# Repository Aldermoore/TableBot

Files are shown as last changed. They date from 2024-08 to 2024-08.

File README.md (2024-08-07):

# TableBot

Repo for the final code, 3d-models and assembly instructions for the TableBot tabletop telepresence robot

**Table of content**

[Components needed](#components-needed)

* [Electronics](#electronics)
* [Hardware](#hardware)
* [Files to 3D print](#files-to-3d-print)

[Assembly instructions](#assembly-instructions)

* [Assembling the head](#assembling-the-head)
* [Assembling the base](#assembling-the-base)

[Installation](#installation)

[Configuration and Running the software](#configuration-and-running-the-software)

<small><i><a href='http://ecotrust-canada.github.io/markdown-toc/'>Table of contents generated with markdown-toc</a></i></small>

---

# ⚠️ **DISCLAIMER: We provide no guarantee that you will produce a working product from following these instructions!**

---

## Components needed

### Electronics

* Raspberry Pi 4

* 7'' touchscreen for Raspberry Pi 

* 180° fish-eye lens USB camera, model ELP-USBFHD01M-L180 

* Jabra Speak 510 conference microphone and speaker

* Servo RDS3115mg

* Stepper Motor 17HS4401 x2

* Adafruit motor shield V1 (V1 is discontinued, use V2 instead at your own risk)

* Arduino Uno

* RGB LED-strip

* Power Banks 5000mAh 2.5A x3 (TB is designed for quite flat batteries, but the battery compartment can be modified to accomodate other battery shapes)

* USB-A cables to connect powerbanks to electronics (these will be cut open during assembly!) 

* A few basic electronic components; Capacitor, diode, breadboard/soldering-board, Jumperwires

### Hardware

* 3D-printer (Prusa Mini or larger) 

* Access to soldering equipment

* Access to silicone casting to create tires

* Tabletop-tennis ball (for the castor wheel)

* Screws and appropriate screwdriver
  
  * Assorted screws for electronics (see pictures)
20240806_121625 (1)
20240806_121608 (1)
20240806_121558 (1)
20240806_121548 (1)
20240806_121401 (1)


## Files to 3D print

All 3d files to build TableBot are available in the TableBot_stl folder. All files should only be printed once, except for the wheels (you might prefer to have two of those).

The wheels have silicone tires, and the folder Silicone_mould includes the necessary files. To produce the mould, print one of each piece. Connect all pieces with a wheel base as the centre, close outer gaps with tape and pour in your silicone mixture. Let the silicone set for some time. Pull apart the mould and repeat for the second wheel.

The original TableBot is printed primarily in PLA, but a few pieces are printed in PETG for better heat resistance and flexibility. This includes:
* Arduino_mount.stl
* RaspberryPi_mount.stl
* Screen_grid.stl

The Diffuser_Plane.stl file should be printed in a clear material to allow light through it.

## Assembly instructions

To build the robot, please have the 3d printed files ready and without supports. The following images may include 3d printed elements that differ from those in the included files, as the files offered in this repository has been updated with any changes made to those shown in the images.

First, build the head, then the base and put the two together in the end.

### Assembling the head
Place nuts in assigned slots on the grid

Attach servo arm using four bolts


Attach the grid to the back of the screen in eight spots

Attach holder for Raspberry Pi using the screws for the heat sink. Use four small nuts to as spacers to ensure the plastic does not touch the Raspberry Pi directly


Connect the display cable to the screen


Flip the Raspberry Pi and connect it to the grid using two bolts


Place the screen in the 3d printed frame. Use four bolts to keep it in place

Install the camera by placing it in the assigned space and use two small screws to keep it in place


Leave the head for now as we build the main body
### Assembling the base
Pad the stepper motors with some felt to reduce vibrations and place them in the assigned slots.


Place four nuts in the assigned spots inside the bottom of the handle.

The neck must be fully wired before attached to the body. Prepare the Jabra speaker, the servo motor, a data cable for the Arduino, a power cable for the Raspberry Pi and a length of male/female jumper wires for the LED strip, one for data, one for power and one for ground.

Before wiring the handle, the Jabra speaker needs to have its wire moved from the front to the back of the main body.

Now send all wires through the handle. Ensure the top of the handle has the wires as shown on the following image. The wire for the servo motor must be moved through the handle to the bottom of the handle.

Before connecting the handle to the base, move the LED jumper wires through the hole in the base of the main body.

Slid the handle into the groved on the top of the main body and secure it using two bolts.

Pull the power cable for the Raspberry Pi through the hole in the bottom of the main body.

Prepare the Arduino motor driver shield.


Combine the 3d printed Arduni base with the Arduino and shield.


Slide the Arduino onto the main body.

Up next secure the connection between the power and Servo motor using a flyback diode.


Connect the servo motor to the Arduino motor driver shield through the flyback diode.

Tug the loose wires into the space below the handle.

Under the main body, pull the power supply chords for the Arduino and Servo motor through the same hole as the power cable for the Raspberry Pi.

Next, prepare the side covers for the main body.

Pull the wires for the wires for the stepper motors through the hole underneath the side piece. Connect them with the closest free wires from the Arduino motor shield by matching the colours.

To secure the side cover, slide it into place while pulling the wires out of the way. Repeat on the other side.

Tug the loose wires into the space above the stepper motors.

At the front of the main body, prepare 3d prints and an LED strip.

Place the LED strip within the slot on the solid piece. To help it along, shape the LED strip through small bends.

Place the 3d printed piece with the LED strip on the front of the main body. Make sure the wires for the LED strip face the centre of the front area when placing it. Connect the LED strip with the jumper wires.


Tug the wires away along the side and place Jabra speaker in the assigned slot with its wires rolled up around its base.

Lightly place the diffuser piece over the LEDs.

Attach the large wheels to the stepper motors.

Underneath the robot attach the ball wheel base with two short wood screws. Once in place, insert the ping-pong ball.


Prepare the back piece and two bolts.

Slide the back piece in place and secure it with the two bolts


Attach the head to the body of the robot using the servo arm and the accompanying bolts. Connect all cables and wires to the Raspberry Pi.

Prepare the back of the head and secure it using four small bolts.


In the front, ensure the jumper wires for power to the Arduino and Servo have USB ends. Insert the three power banks into the slots in the front of the main body.

Connect a power bank to each wire.

Close the drawer while tugging any remaining lose wires into the drawer space.

### Attach the head



## Installation

Flash the code in `code / motorcontroller` to the Arduino Uno. 

The remaining code must be moved to the Raspberry Pi. Using git, make sure to clone into the home folder! 

Follow the build and install instructions in `code / video4linux-custom`

From `code / video4linux-custom` run the script called `setupeverything.sh`. 
**NOTE:** The script expects that the path to the files is `~/TableBot/code/front-end-webrtc/server.sh` and `~/TableBot/code/websocket-server/websocketServer.py`. If you have not cloned the repo to the home folder, or have used other means to move the code to the Raspberry Pi, then update the paths on lines 14 and 15 in the `setupeverything.sh` script to reflect this change! 

## Configuration and Running the software

Connect a keyboard and mouse to the Raspberry Pi. 

Connect the Pi to your Wifi network. Note the IP address of the Pi. 

Run the `setupEverything.sh` script. 

In a browser (Tested with Google Chrome, not working with Firefox!), go to the Pi's IP address, port 5

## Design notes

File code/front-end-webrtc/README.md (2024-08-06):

# uv4l-webrtc-front-end

UV4L Webrtc Front-End Source Code

Original source code of UV4L WebRTC front end. No code changes, only split html, js and css. Original code by [https://www.linux-projects.org](https://www.linux-projects.org/)

This code should be downloaded to the Raspberry Pi used in TableBot! 

#

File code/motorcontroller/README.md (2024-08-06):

# Motor-Controller

Motor controller code for Arduino. The code assumes that the Adafruit Motor Shield (AMS) V1 is connected to the arduino, and that the motors are wired as described below. 

**It is NOT tested with the Motor Shield V2**

## Overview of files

`tablebotWheelset/tablebotWheelset.ino` is the one that should be uploaded to the Arduino to work with TableBot. 

## Wiring Arduino and motors

1. Connect the arduino motor shield to the arduino

2. Connect the stepper motors in the following way
   
   1. Left stepper is connected to M3 & M4, while right stepper is connected to M1 & M2. 
   
   2. With the specific set of motor terminals facing you, the steppers are wired up in the order: 
      Orange, Brown, Red, Yellow
      So the leftmost terminal connects the orange wire on the stepper, while the rightmost terminal connects the yellow wire on the stepper. Fuck this up and the steppers will *not* drive correctly! 
   
   3. Left stepper obviously need to be on the left side of the robot chassis (duh) 

3. Connect the servo to the first servo port labeled SER1 or SERVO_1 or similar.

4. You should be all done for now, except for the fact that the steppers draw too much power so they might shut down the arduino which is kind of a problem for future us...

## Powering the motors

The steppers can be powered from external power via the `EXT_PWR`  connectors. Wire up a bettery to this port, e.g. by cutting a USB-cable and soldering some jumper wire ends to the power and ground leads of the cable. 

Additionally the `PWRJMP` jumper should be removed from the board when using external power.

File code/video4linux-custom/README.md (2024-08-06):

v4l2loopback - a kernel module to create V4L2 loopback devices
==============================================================

This module allows you to create "virtual video devices".
Normal (v4l2) applications will read these devices as if they were ordinary
video devices, but the video will not be read from e.g. a capture card but
instead it is generated by another application.
This allows you for instance to apply some nifty video effects on your
Skype video...
It also allows some more serious things (e.g. I've been using it to add
streaming capabilities to an application by the means of hooking GStreamer into
the loopback devices).

# NEWS

To get the main features of each new release, see the NEWS file.
You could also have a look at the ChangeLog (which gets automatically generated and might
only be of limited use...

# ISSUES

For current issues, checkout https://github.com/umlaeute/v4l2loopback/issues
Please use the issue-tracker for reporting any problems.

Before you create a new ticket in our issue tracker, please make sure that you have read
*this* document and followed any instructions found within.

Also, please search the issue-tracker *before* reporting any problems: it's much better
to add your information to an existing ticket than to create a new ticket with essentially
the same information.

## SEEKING HELP

The issue tracker is meant to track specific bugs in the code (and new features).
However, it is ill-suited as a user support forum.

If you have general questions or problems, please use the `v4l2loopback` tag
on [Unix & Linux](https://unix.stackexchange.com/questions/tagged/v4l2loopback) instead:
https://unix.stackexchange.com/questions/tagged/v4l2loopback

# DEPENDENCIES

In order to build (compile,...) anything, you must have a *working* build-environment
(compiler, GNU make,...).
The kernel can be somewhat picky if you try to load a module that was compiled with
a different compiler as was used to compile the kernel itself.
So make sure to have the right compiler in place.

The v4l2loopback module is a *kernel module*.
In order to build it, you *must have* the kernel headers installed that match
the linux kernel with which you want to use the module (in most cases this will
be the kernel that you are currently running).
Please note, that kernel headers and kernel image must have *exactly the same* version.
For example, `3.18.0-trunk-rpi` is a different version than `3.18.7-v7+`, even though
the first few numbers are the same.
(Modules will be incompatible if the versions don't match. If you are lucky, the module will
simply refuse to load. If you are unlucky, your computer will spit in your eye or do worse.)

There are distribution-specific differences on how to get the correct kernel headers
(or to install a compilation toolchain).
Documenting all those possibilities would go far beyond the scope of `v4l2loopback`.
Please understand that we cannot provide support for questions regarding dependencies.

# BUILD

To build the kernel module, run:

    $ make

This should give you a file named "v4l2loopback.ko", which is the kernel module

## BUILD AGAIN

You cannot load a module built for a specific version of the kernel into another version of the kernel.
So, if you have successfully built the module previously and have updated your kernel (and the matching headers)
In the meantime, you really must clean the build before re-compiling the module.
So run this *before* starting the build again:

    $ make clean

# INSTALL

To install the module, run "make install" (you might have to be 'root' to have
all necessary permissions to install the module).

If your system has "sudo", do:

    $ make && sudo make install
    $ sudo depmod -a

If your system lacks "sudo", do:

    $ make
    $ su
    (enter root password)
    # make install
    # depmod -a
    # exit

(The `depmod -a` call will re-calculate module dependencies, in order to
automatically load additional kernel modules required by v4l2loopback.
The call may not be necessary on modern systems.)

See below for [distribution-specific build instructions](#DISTRIBUTIONS)
or when using frameworks like [`DKMS`](#DKMS).

# RUN

Load the v4l2loopback module as root :

    # modprobe v4l2loopback

Using `sudo` use:

    $ sudo modprobe v4l2loopback

You can check which loopback devices are created by listing contents of
`/sys/devices/virtual/video4linux` directory. E.g. if there are two
`v4l2loopback` devices `/dev/video0` and `/dev/video3` you would get:

    $ ls -1 /sys/devices/virtual/video4linux
    video0
    video3

These devices are ready to accept contents to show.

Tested feeders:

- GStreamer-1.0: using the  "v4l2sink" element
- Gem(>=0.93) using the "recordV4L2" plugin

In theory most programs capable of _writing to_ a v4l2 device should work.

The data sent to the v4l2loopback device can then be read by any v4l2-capable
application.

You can find a number of scenarios on the wiki at
    http://github.com/umlaeute/v4l2loopback/wiki

## Troubleshooting

If you have a secure-boot enabled kernel, you might not be able to simply build a kernel module and insert it.
(You will get **SSL error**s when building the module.)
This is actually a security feature (as it prevents malicious code to be inserted into kernel-space).

If you are not allowed to insert the kernel module (running `modprobe`, or `insmod`), you have a few options
(consult your distribution's documentation on how to perform any of these steps):

- disable secure-boot and reboot
- sign the module binary with a whitelisted key (this probably only applies if you are creating a distribution)

You could also just try building the module [via `DKMS`](#DKMS), and hope that it does all the magic for you.

# OPTIONS

If you need several independent loopback devices, you can pass the "devices"
option, when loading the module; e.g.

    # modprobe v4l2loopback devices=4

Will give you 4 loopback devices (e.g. `/dev/video1` ... `/dev/video5`)

You can also specify the device IDs manually; e.g.

    # modprobe v4l2loopback video_nr=3,4,7

Will create 3 devices (`/dev/video3`, `/dev/video4` & `/dev/video7`)

    # modprobe v4l2loopback video_nr=3,4,7 card_label="device number 3","the number four","the last one"

Will create 3 devices with the card names passed as the second parameter:

- `/dev/video3` -> *device number 3*
- `/dev/video4` -> *the number four*
- `/dev/video7` -> *the last one*

If you encounter problems detecting your device with Chrome/WebRTC you can try 'exclusive_caps' mode:

    # modprobe v4l2loopback exclusive_caps=1

This will enable 'exclusive_caps' mode that only reports CAPTURE/OUTPUT capabilities exclusively.
The newly created device will announce OUTPUT capabilities only (so ordinary webcam applications
(including Chrome) won't see it). As soon as you have attached a producer to the device, it will
start announcing CAPTURE capabilities only (so applications that refuse to open devices that have
other capabilities apart from capturing can open it too.)

## CHANGING OPTIONS

Options that you provided when loading the module (e.g. via `modprobe`) cannot be easily changed
on the fly.
In order to change these options, you must first unload the module with `rmmod`
(which will only work if no application is any longer accessing one of the loopback devices)
and then load it again (with the new options).

See also the section about [DYNAMIC DEVICE MANAGEMENT](#dynamic-device-management).

# ATTRIBUTES

you can set and/or query some per-device attributes via sysfs, in a human
readable format. See `/sys/devices/virtual/video4linux/video*/`

also there are some V4L2 controls that you can list with

    $ v4l2-ctl -d /dev/video0 -l

- `keep_format(0/1)`: while set to 1, once negotiated format will be fixed forever,
  
                  until the setting is set back to 0

- `sustain_framerate(0/1)`: if set to 1, nominal device fps will be ensured by means
  
                        of frame duplication when needed

- `timeout(integer)`: if >0, will cause a timeout picture (a null frame, by default)
  
                  to be displayed after (value) msecs of missing input

- `timeout_image_io(0/1)`: if set to 1, the next opener will write to timeout frame
  
                       buffer

# CHANGING THE RUNTIME BEHAVIOUR

## FORCING FPS

    $ v4l2loopback-ctl set-fps /dev/video0 25

or

    $ echo '@100' | sudo tee /sys/devices/virtual/video4linux/video0/format

## FORCING FORMAT

    $ v4l2loopback-ctl set-caps /dev/video0 "UYVY:640x480"

Please note that *GStreamer-style caps* (e.g. `video/x-raw,format=UYVY,width=640,height=480`) or no longer supported!

## SETTING STREAM TIMEOUT

You can define a timeout (in milliseconds), after which the loopback device will start outputting NULL frames,
if the producer suddenly stopped.

```
$ v4l2-ctl -d /dev/video0 -c timeout=3000
```

Alternatively, you can calso provide a timeout-image, which will be displayed (instead of the NULL frames),
if the producer doesn't send any new frames for a given period:

```
$ v4l2loopback-ctl set-timeout-image -t 3000 /dev/video0 service-unavailable.png
(this currently requires GStreamer 1.0 installed)
```

## DYNAMIC DEVICE MANAGEMENT

You can create (and delete) loopback devices on the fly, using the `add` (resp. `delete`) commands of the `v4l2loopback-ctl` utility.

When creating a new device, module options might be ignored. So you must specify them explicitly.

To create a new device `/dev/video7` that has a label "loopy doopy", use:

```
$ sudo v4l2loopback-ctl add -n "loopy doopy" /dev/video7
```

Deleting devices is as simple as:

```
$ sudo v4l2loopback-ctl delete /dev/video7
```

# KERNELs

The original module has been developed for linux-2.6.28;
I don't have a system with such an old kernel anymore, so I don't know whether
it still works.
Further development has been done mainly on linux-2.6.32 and linux-2.6.35, with
newer kernels being continually tested as they enter Debian.

Support:

- > = <kbd>5.0.0</kbd>        should work
- > = <kbd>4.0.0</kbd>        should work
- > = <kbd>3.0.0</kbd>        might work
- << <kbd>3.0.0</kbd>        may work (has not been tested in ages)
- <= <kbd>2.6.37</kbd>        will definitely NOT work

# DISTRIBUTIONS

v4l2loopack is now (since 2010-10-13) available as a Debian-package.
https://packages.debian.org/source/stable/v4l2loopback

This means, that it is also part of Debian-derived distributions, including
Ubuntu (starting with natty).
The most convenient way is to install the package "v4l2loopback-dkms":

    # apt-get install v4l2loopback-dkms

This should automatically build and install the module for your current kernel
(provided you have the matching kernel-headers installed).
Another option is to install the "v4l2loopback-source" package.
In this case you should be able to simply do (as root):

    # apt-get install v4l2loopback-source module-assistant
    # module-assistant auto-install v4l2loopback-source

# DKMS

The *Dynamic Kernel Module Support framework* (DKMS) is designed to allow
individual kernel modules to be upgraded without changing the whole kernel.
It is also very easy to rebuild modules as you upgrade kernels.

If your distribution doesn't provide `v4l2loopback`-packages (or they are too old)
and you are experiencing troubles with code-signing, you probably should try this.

E.g. to build the v4l2loopback-v0.12.5 (but check the webpage for newer releases first!),
use something like the following (you might need to run the `dkms` commands as superuser/root):

```
version=0.12.5
# download and extract the tarball (tar requires superuser privileges)
curl -L https://github.com/umlaeute/v4l2loopback/archive/v${version}.tar.gz | tar xvz -C /usr/src
# build and install the DKMS-module (requires superuser privileges)
dkms add -m v4l2loopback -v ${version}
dkms build -m v4l2loopback -v ${version}
dkms install -m v4l2loopback -v ${version}
```

| distribution | dependencies |
| --- | --- |
| Fedora,... | gcc kernel-devel dkms |
| Debian, Ubuntu,... | dkms |

Note that using this method will NOT install the v4l2loopback-ctl tool, you will have to do it yourself!

# LOAD THE MODULE AT BOOT

One can avoid manually loading the module by letting systemd load the module
at boot, by creating a file `/etc/modules-load.d/v4l2loopback.conf` with just
the name of the module:

```
v4l2loopback
```

This is especially convenient when `v4l2loopback` is installed with DKMS or with
a package provided by your Linux distribution.

If needed, one can specify default module options by creating
`/etc/modprobe.d/v4l2loopback.conf` in the following form:

```
options v4l2loopback video_nr=3,4,7
options v4l2loopback card_label="device number 3,the number four,the last one"
```

One can only add one option per line. These options also become the defaults when
manually calling `modprobe v4l2loopback`. Note that the double quotes can only
be used at the beginning and the end of the option's value, as opposed to when
they are specified on the command line.

If your system boots with an initial ramdisk, which is the case for most
modern distributions, you need to update this ramdisk with the settings above,
before they take effect at boot time. In Ubuntu, this image is updated with
`sudo update-initramfs`. The equivalent on Fedora is `sudo dracut -f`.

# DOWNLOAD

The most up-to-date version of this module can be found at
http://github.com/umlaeute/v4l2loopback/.

# LICENSE/COPYING

- Copyright (c) 2010-2021 IOhannes m zmoelnig

- Copyright (c) 2016 Gavin Qiu

- Copyright (c) 2016 George Chriss

- Copyright (c) 2014-2015 Tasos Sahanidis

- Copyright (c) 2012-2015 Yusuke Ohshima

- Copyright (c) 2015 Kurt Kiefer

- Copyright (c) 2015 Michel Promonet

- Copyright (c) 2015 Paul Brook

- Copyright (c) 2015 Tom Zerucha

- Copyright (c) 2013 Aidan Thornton

- Copyright (c) 2013 Anatolij Gustschin

- Copyright (c) 2012 Ted Mielczarek

- Copyright (c) 2012 Anton Novikov

- Copyright (c) 2011 Stefan Diewald

- Copyright (c) 2010 Scott Maines

- Copyright (c) 2009 Gorinich Zmey

- Copyright (c) 2005-2009 Vasily Levin
  
    This package is free software; you can redistribute it and/or modify
    it under the terms of the GNU General Public License as published by
    the Free Software Foundation; either version 2 of the License, or
    (at your option) any later version.
  
    This package is distributed in the hope that it will be useful,
    but WITHOUT ANY WARRANTY; without even the implied warranty of
    MERCHANTABILITY or FITNESS FOR A PARTICULAR PURPOSE.  See the
    GNU General Public License for more details.
  
    You should have received a copy of the GNU General Public License
    along with this program. If not, see <http://www.gnu.org/licenses/>.

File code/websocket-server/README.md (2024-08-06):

# Websocket-Server

Websocket server for TableBot 2.0 

THe websocket is responsible for recieving control messages and relay them to the motor controller - an Arduino connected to `/dev/ttyACM0` using the Adafruit Motor Shield (AMS). The data is also relayed to an led indicator script that will correctly display the pilot's direction of attention on the robot. 

The main file is `websocketServer.py`. The code expect that an Arduino is connected to `/dev/ttyACM0`, otherwise it won't work. All messages received through the websocket are logged to a file called `tablebot2.log`

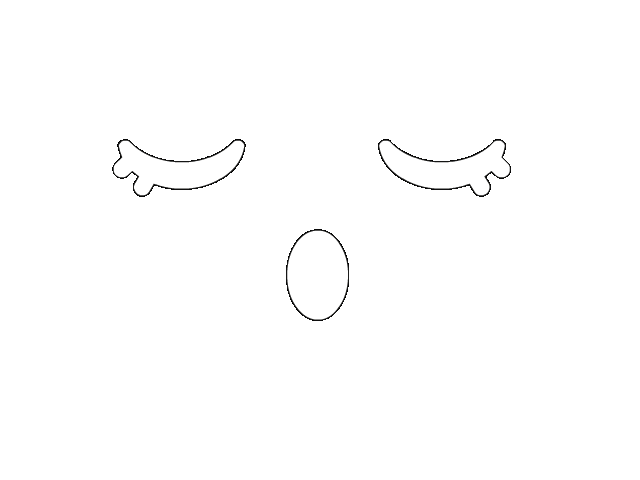
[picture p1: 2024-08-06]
code/front-end-webrtc/sleeping_animation.gif

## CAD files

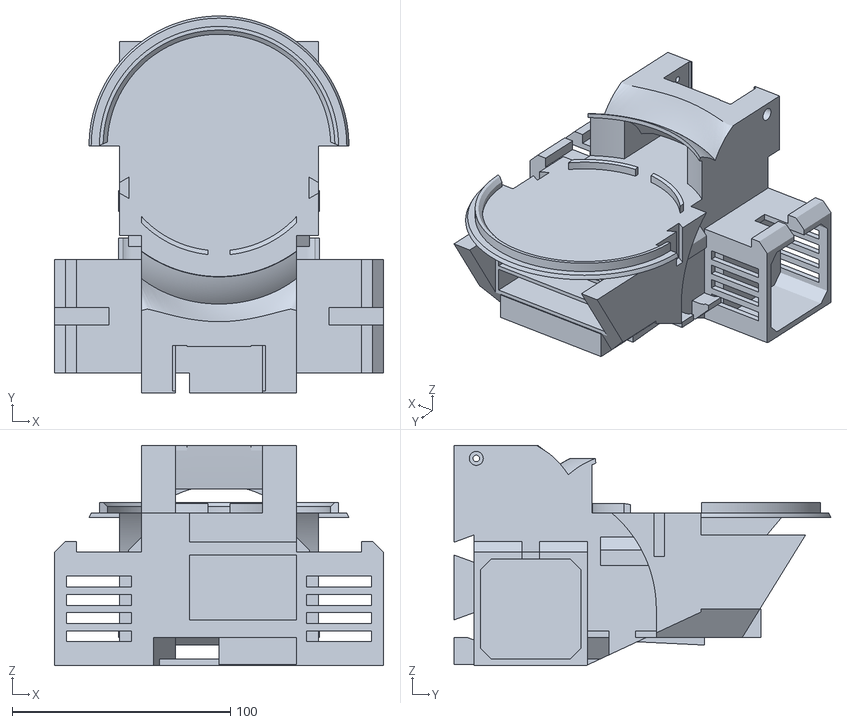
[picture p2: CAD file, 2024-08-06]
TableBot_stl/Main_body.stl
150.8 x 172.8 x 101.0

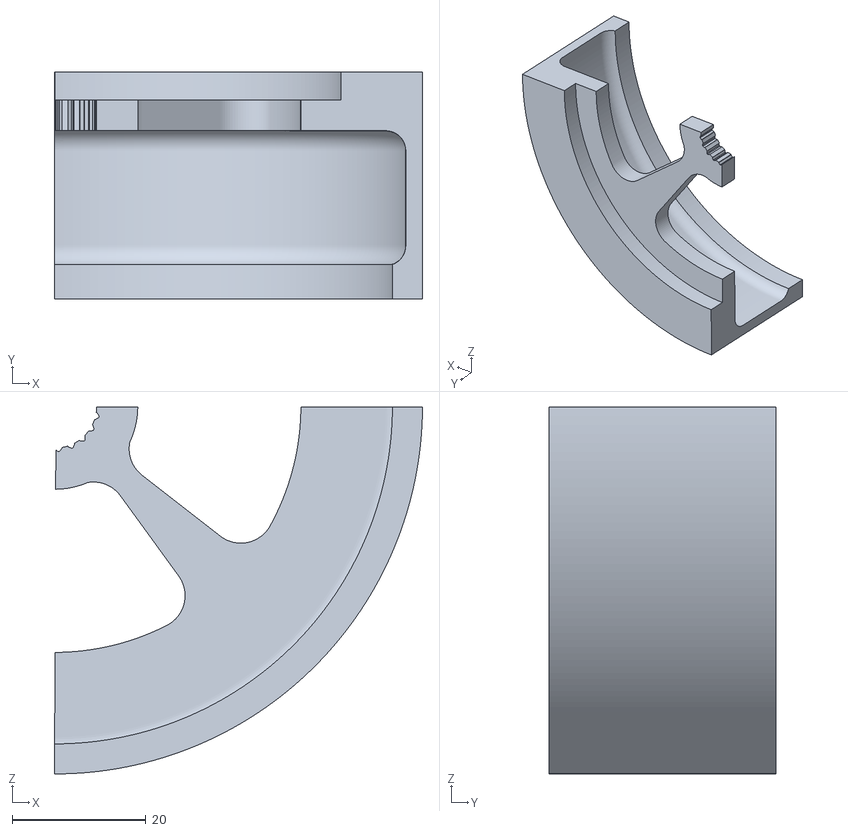
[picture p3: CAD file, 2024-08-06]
Silicone_mould/casting-side2.stl
55.1 x 34.0 x 54.9

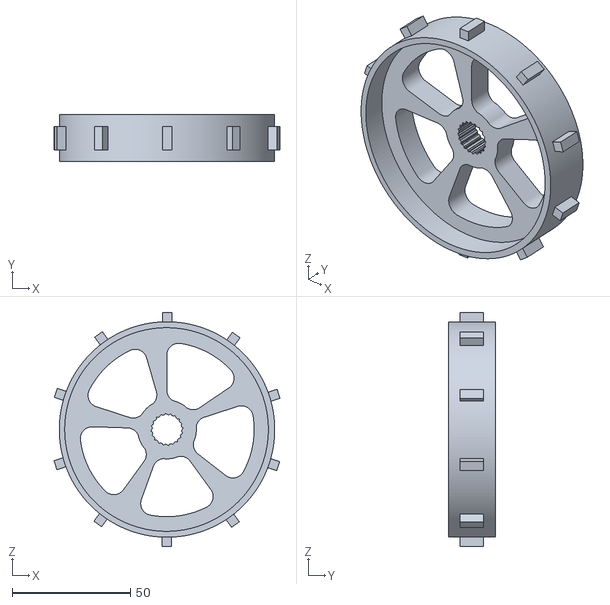
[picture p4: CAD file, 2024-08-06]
TableBot_stl/wheel.stl
95.4 x 19.8 x 99.0

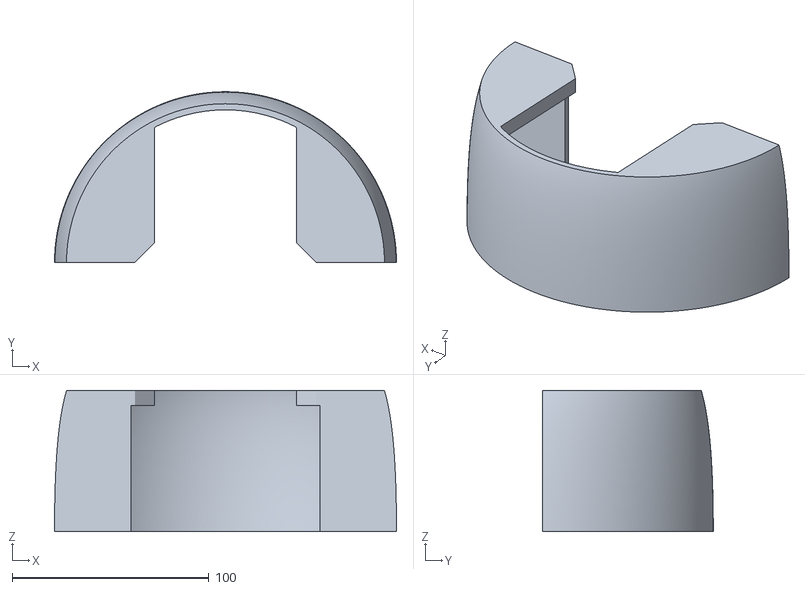
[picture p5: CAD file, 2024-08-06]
TableBot_stl/Front_curve.stl
174.0 x 86.8 x 71.8

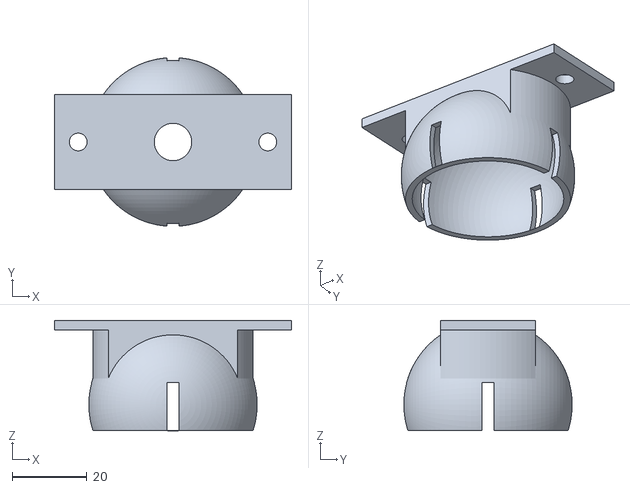
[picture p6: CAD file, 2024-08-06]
TableBot_stl/Ping-pong_wheel.stl
63.5 x 45.1 x 29.6

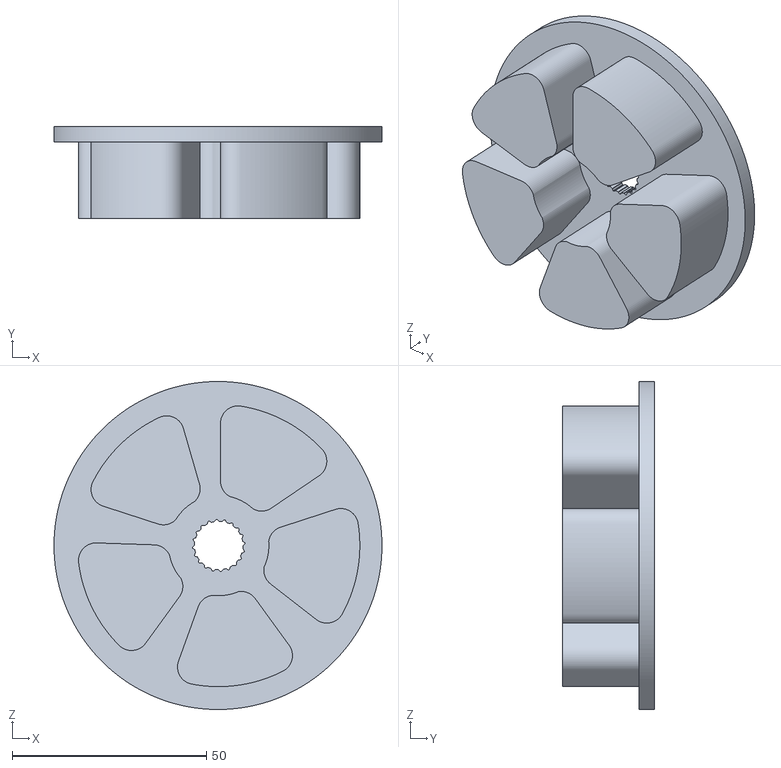
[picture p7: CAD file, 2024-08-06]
Silicone_mould/casting-bottom.stl
84.4 x 23.8 x 84.4

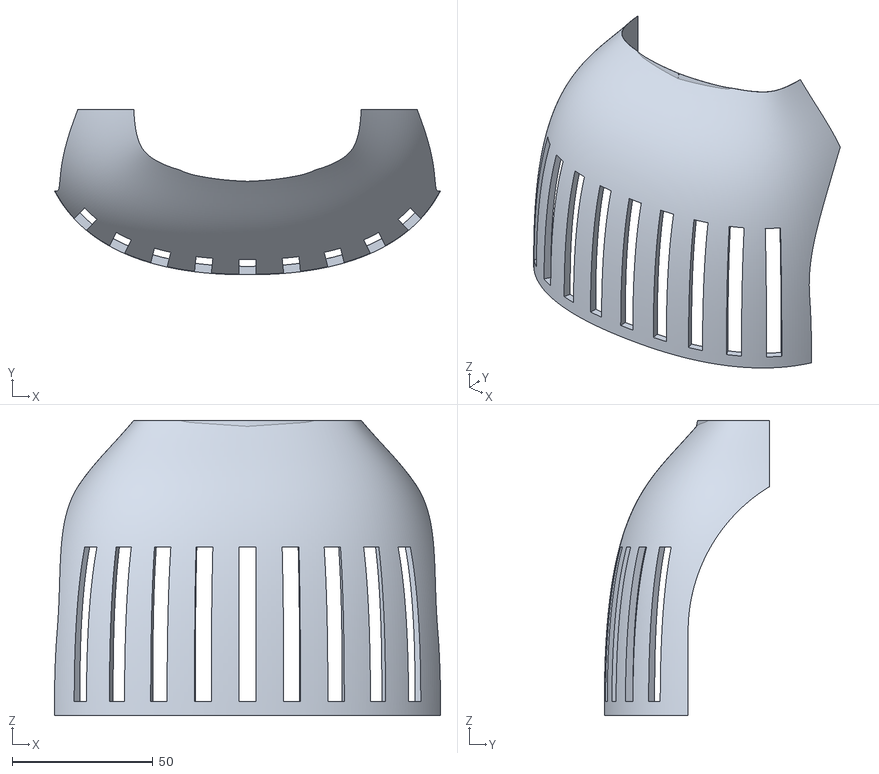
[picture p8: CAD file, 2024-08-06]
TableBot_stl/Shell_back.stl
137.2 x 58.8 x 105.0

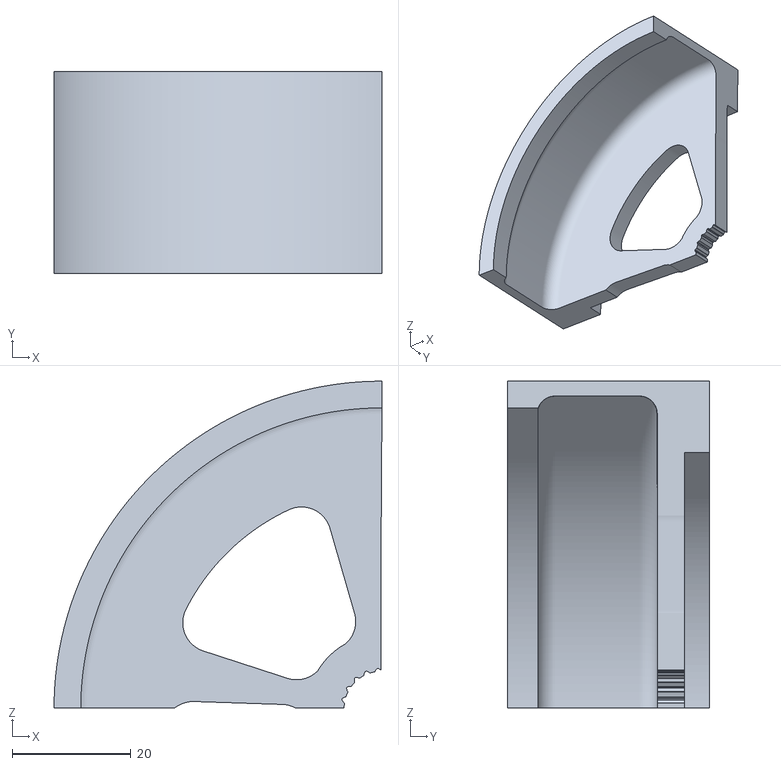
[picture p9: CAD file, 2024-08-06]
Silicone_mould/casting-side3.stl
55.1 x 34.0 x 54.9

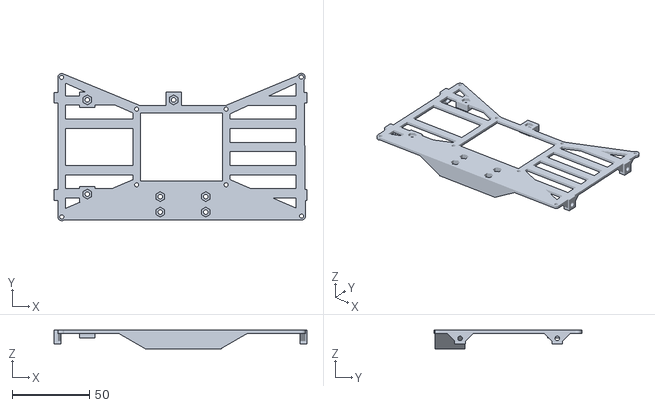
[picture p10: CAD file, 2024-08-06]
TableBot_stl/Screen_grid.stl
163.9 x 95.6 x 12.0

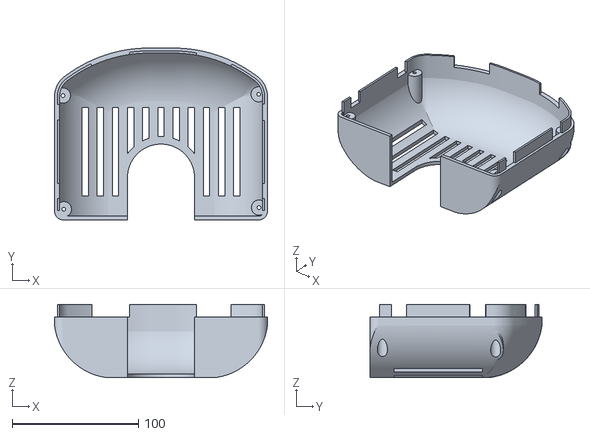
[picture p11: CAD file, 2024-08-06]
TableBot_stl/Head_back.stl
168.5 x 136.0 x 58.0

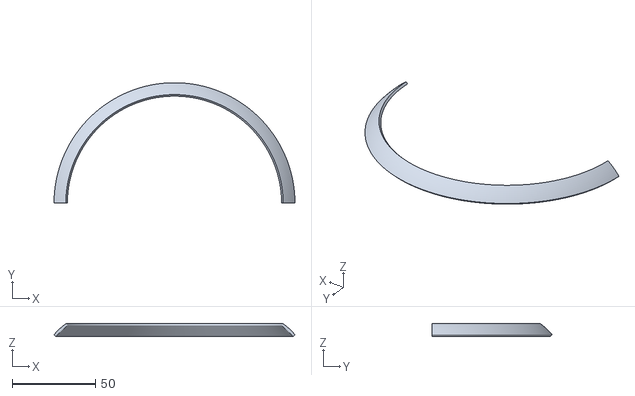
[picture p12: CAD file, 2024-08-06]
TableBot_stl/Diffuser_Plane.stl
144.4 x 72.2 x 7.54

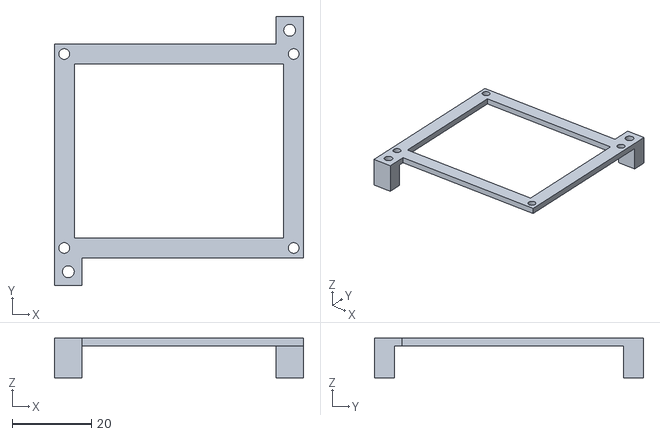
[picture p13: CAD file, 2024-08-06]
TableBot_stl/RaspberryPi_mount.stl
62.9 x 68.0 x 10.0

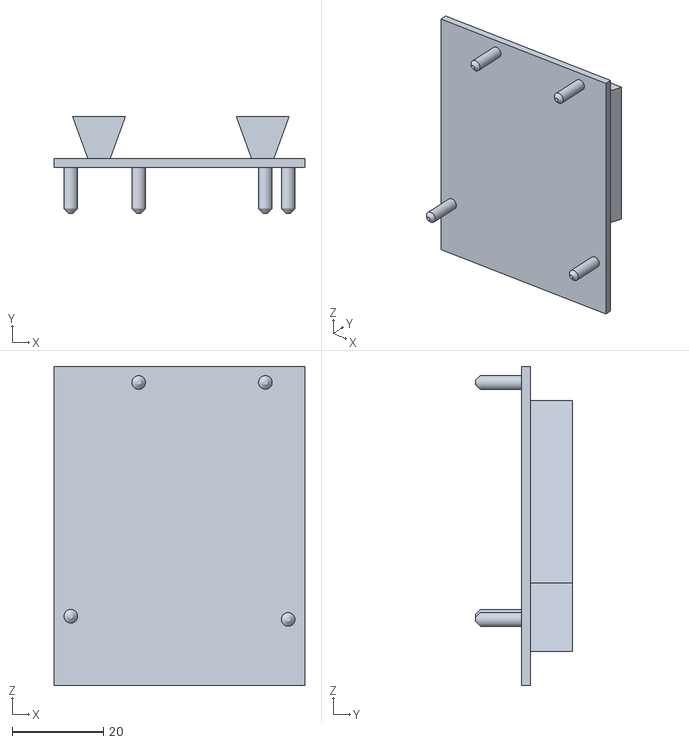
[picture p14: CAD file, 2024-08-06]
TableBot_stl/Arduino_mount.stl
55.0 x 21.2 x 70.0

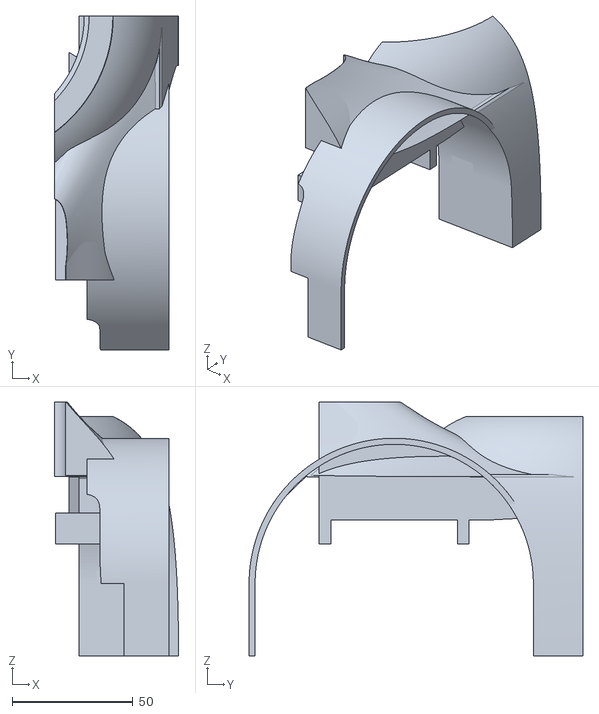
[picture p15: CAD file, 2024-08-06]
TableBot_stl/Side_2.stl
51.3 x 138.0 x 105.0

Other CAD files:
Silicone_mould/casting-side1.stl
Silicone_mould/casting-side4.stl
TableBot_stl/Screen_frame.stl
TableBot_stl/LED_holder.stl
TableBot_stl/Side_1.stl

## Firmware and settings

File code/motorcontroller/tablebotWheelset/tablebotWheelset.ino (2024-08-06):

/*
CODE FOR DRIVING THE TABLEBOT 2.0
TableBot 2.0 uses the Adafruit Motor Driver Shield (v1)

(c) The Authors of TableBot
*/

/***** Things to finetune here *****/
const float wheelsetDistance = 19; // Wheelset distance in cm
const float wheelDiameter = 10.45; // Wheel diameter in cm
const double stepperMaxSpeed = 300; // Max steps/s for the steppers 
const double stepperAcceletation = 200; // How fast the steppers reach max speed (no. steps it takes?)
const int servoDelay = 25; // Delay im ms between each step in the servo
const int servoMax = 120; // Maximum angle of the servo, looking up. 
const int servoMin = 40; // Minimum angle of the servo, looking down. 
/***** No more things to finetune *****/
 
/*
Enter data in the serial monitor in this way: 
  <driveVal,turnVal,tiltVal>

# driveVal is either 'forward', 'backward' or 'stop' for commands, 
  without the quotes! Any other word will be ignored. 

# turnVal is the number of degrees you wish to turn in place. 
  Positive means turn to the left, negative means turn to the right. 
  0 means no turning. 

# tiltVal is a number corresponding to the position of a servo motor. 
  The number should be <=150, >=90. Numbers outside this range are set 
  to the closest number in the range, e.g. too large number -> 150. 
  Except for 0, which is the don't-change-the-tilt number

e.g. to rotate 120 degrees to the left while tilting the servo down: 
  <stop,120,150>
To stop the movement of the steppers: 
  <stop,0,0>

NOTE: Moving forward or backward while rotating is not an option. 
      The linear movement will terminate followed by the rotation 
      in a funky way. 
      TODO: Fix this ^^
*/


#include <Arduino.h>
#include <AccelStepper.h>
#include <AFMotor.h>
#include <Servo.h>

/* 
Field variables for receiving data from the serial connection
*/
const byte numChars = 32;
char receivedChars[numChars];
char tempChars[numChars];  // temporary array for use when parsing
  // variables to hold the parsed data
char driveVal[numChars] = { 0 };
int turnVal = 0;
int tiltVal = 0;
boolean newData = false;

/* 
Wheelset consts for calculating rotation
*/
const float w = wheelsetDistance; // wheelset distance (cm)
const float dia = wheelDiameter;  // wheel diameter (cm) 
const float rad = dia / 2;        // wheel radius (cm)
const float cir = dia * PI;       // wheel circumference (cm)

/*
servostuff
*/
Servo servo;         // create servo object to control a servo
int pos = 90;        // variable to store the servo's current position
unsigned long lastServoMove = 0;
int servoGoalPos = 90;  // Variable for holding the desired servo position


/*
Setting up stepper motors using the AccelStepper library
*/
// two stepper motors one on each port
AF_Stepper motor1(200, 1);
AF_Stepper motor2(200, 2);

// you can change these to DOUBLE or INTERLEAVE or MICROSTEP!
// wrappers for the first motor!
void forwardstep1() {
  motor1.onestep(FORWARD, INTERLEAVE);
}
void backwardstep1() {
  motor1.onestep(BACKWARD, INTERLEAVE);
}
// wrappers for the second motor!
void forwardstep2() {
  motor2.onestep(FORWARD, INTERLEAVE);
}
void backwardstep2() {
  motor2.onestep(BACKWARD, INTERLEAVE);
}

// Motor shield has two motor ports, now we'll wrap them in an AccelStepper object
AccelStepper rightStepper(forwardstep1, backwardstep1);
AccelStepper leftStepper(forwardstep2, backwardstep2);



void setup() {
  Serial.begin(115200);
  
  servo.attach(10);                     // attaches the servo on pin 10 to the servo object
  servo.write(pos);                     // Sets the servo the current position as the start
  rightStepper.setMaxSpeed(stepperMaxSpeed);
  rightStepper.setAcceleration(stepperAcceletation);
  leftStepper.setMaxSpeed(stepperMaxSpeed);
  leftStepper.setAcceleration(stepperAcceletation);
}

// Scoop di loop
void loop() {
  // Read data from the serial connection
  recvWithStartEndMarkers();
  if (newData == true) {
    strcpy(tempChars, receivedChars);
    // this temporary copy is necessary to protect the original data
    // because strtok() used in parseData() replaces the commas with \0
    parseData();
    showParsedData();
    if (strcmp(driveVal, "forward") == 0) {
      Serial.println("Moving forward");
      forward();
    } else if (strcmp(driveVal, "backward") == 0) {
      Serial.println("Moving backward");
      backward();
    } else if (strcmp(driveVal, "stop") == 0) {
      Serial.println("Stopping");
      stopSteppers();
    }
    // If none of the above, new movements for the steppers
    // will not be set, i.e. any other string is ignored
    if (turnVal != 0) {
      Serial.println("Turning!");
      turn(turnVal);
    }
    if (tiltVal != 0) {
      Serial.print("Tilting ");
      Serial.print(tiltVal);
      Serial.print(" degrees");
      servoGoalPos = pos + tiltVal; 
      if (servoGoalPos > servoMax) { servoGoalPos = servoMax; }
      if (servoGoalPos < servoMin) { servoGoalPos = servoMin; }
      Serial.print(", towards ");
      Serial.println(servoGoalPos);
    }
    newData = false;
  }

  if (pos != servoGoalPos) {
    if ((millis() - lastServoMove) > servoDelay)  //if more than servoDelay passed since the last servo move
    {
      tilt();
    }
  }

  rightStepper.run();
  leftStepper.run();
}

/********** Serial functions **********/
/*  Shamelessly aquired from the web  */
void recvWithStartEndMarkers() {
  static boolean recvInProgress = false;
  static byte ndx = 0;
  char startMarker = '<';
  char endMarker = '>';
  char rc;

  while (Serial.available() > 0 && newData == false) {
    rc = Serial.read();

    if (recvInProgress == true) {
      if (rc != endMarker) {
        receivedChars[ndx] = rc;
        ndx++;
        if (ndx >= numChars) {
          ndx = numChars - 1;
        }
      } else {
        receivedChars[ndx] = '\0';  // terminate the string
        recvInProgress = false;
        ndx = 0;
        newData = true;
      }
    }

    else if (rc == startMarker) {
      recvInProgress = true;
    }
  }
}

void parseData() {  // split the data into its parts

  char* strtokIndx;  // this is used by strtok() as an index

  strtokIndx = strtok(tempChars, ",");  // get the first part - the string
  strcpy(driveVal, strtokIndx);         // copy it to messageFromPC

  strtokIndx = strtok(NULL, ",");  // this continues where the previous call left off
  turnVal = atoi(strtokIndx);      // convert this part to an integer

  strtokIndx = strtok(NULL, ",");
  tiltVal = atoi(strtokIndx);  // convert this part to a float
}

void showParsedData() {
  Serial.print("driveVal ");
  Serial.println(driveVal);
  Serial.print("turnVal ");
  Serial.println(turnVal);
  Serial.print("tiltVal ");
  Serial.println(tiltVal);
}

/********** Stepper functions **********/
/*   These should be selfexplanatory   */
void forward() {
  rightStepper.move(240000);
  leftStepper.move(240000);
}

void backward() {
  rightStepper.move(-240000);
  leftStepper.move(-240000);
}

void stopSteppers() {
  rightStepper.stop();
  leftStepper.stop();
}

/*
Calculates the number of steps a pair of stepper motor configured in 
differential steering need to step to rotate the chassis the given 
angle in degrees.
Then it sets the servos to move tha calculated amount of whole steps. 
TODO: Clean this calculation: There is no need to go from degrees to radians and back again...
*/
void turn(int degrees) {
  int deg = degrees;  // Degrees you wish to rotate (positive is right, negative left)
  // Stepper consts
  float steps = 400.0;            // No. steps in stepper motor (INTERLEAVE setting)
  float d_steps = 360.0 / steps;  // rotation per step.

  // Calculating distance the wheels need to travel to rotate deg
  float r = deg / 180.0 * PI;  // calculate radians from degrees
  float d = r * w;             // calculate distance both wheels need to travel
  float left = d / 2;          // calculate distance for left wheel
  float right = -left;         // right wheel is reverse of left wheel
  // Calculating the angle the wheels need to rotate for the previously calculated distance
  float angR = left / rad;           // angle wheels need to rotate in radians
  float angD = angR * (180.0 / PI);  // angle wheels need to rotate in degrees

  float stepsToTurn = angD / d_steps;  // Calculate no. steps each wheel need to turn
  int leftSteps = floor(stepsToTurn + 0.5);
  int rightSteps = floor(-stepsToTurn + 0.5);

  Serial.print("Wheels go brrrrr ");
  Serial.print(leftSteps);
  Serial.println(" steps");

  leftStepper.move(leftSteps);
  rightStepper.move(rightSteps);
}

/********** Servo functions **********/

/*
Move the servo one step in the direction of servoGoalPos
*/
void tilt() {
  Serial.println("Tilting one step");
  servo.write(pos);
  lastServoMove = millis();  //reset the timer
  if (pos < servoGoalPos) {
    pos += 1;
  } else {
    pos -= 1;
  }
}

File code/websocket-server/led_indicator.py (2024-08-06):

#!/usr/bin/env python3
"""
Code for controlling the LED strip on TableBot 2.  
"""
import threading
import ctypes
import time
import board
import neopixel
from itertools import filterfalse

##### VARIABLES TO CALIBRATE #####
led_delay = 0.3 # Maybe the led delay needs to be dynamic as the robot moves, since it accelerates and decelerates...
##### END OF CALIBRATION #####

# Queue to hold the current thread
movement_queue = []

# pixels = [0,1,2,3,4,5,6,7,8,9,10,11,12] # this is only here for test reasons

minDeg = -90
maxDeg = 90
num_led = 13
old_leds_to_be_on = []

pixel_pin = board.D21
order = neopixel.GRB
pixels = neopixel.NeoPixel(pixel_pin, num_led, brightness = 0.5, pixel_order = order)

pixels.fill((10,10,10))

"""
Shows the pilot's gaze / locus of attention when using shift+mouse_over
"""
def show_gaze(pos: int, led_num: int, led_state: bool): 
    #led = number_remapper(pos,0,24,0,12)
    led = pos
    print("step 1", led)
    led_num = int(led_num)
    leds = calc_leds_to_be_on(led, led_num)
    print("step 2", leds)
    turn_on_leds(leds, led_state)

"""
Lights of the specificed LEDs
"""
def turn_on_leds(leds_to_be_on, led_state):
    global old_leds_to_be_on
    print(leds_to_be_on)
    if(leds_to_be_on != old_leds_to_be_on):
        old_leds_to_be_on = leds_to_be_on
        pixels.fill((10,10,10))
        for p in leds_to_be_on:
            pixels[p] = (210, 210, 210)
            
    elif(leds_to_be_on == old_leds_to_be_on and led_state == True):
        pixels.fill((10,10,10))
        for p in leds_to_be_on:
            pixels[p] = (210, 210, 210)


"""
Calculates which LEDs should be on as specificed by which LED is in the center, and how many LEDs to turn on in total. Will always be an odd number as one LED must be in the center. 
"""
def calc_leds_to_be_on(led: int, led_num: int):
    if(led >= num_led):
        led = num_led-1
    if(led < 0):
        led = 0
    leds_to_be_on = calc_leds(led,led_num)
    # Limiting the leds to be within the led-strip, so some values might be cut off if we are near the end of the strip! 
    leds_to_be_on[:] = [tup for tup in leds_to_be_on if determine(tup)]
    return leds_to_be_on

"""helper function to check in an LED index is out of bound."""
def determine(val: int) -> bool: 
    if val < 0 or val > num_led-1:
        return False
    else: return True

"""
Animates the LED strip from the LED closest to degrees [-90, 90] so that the number of LEDs specificed by led_num, rounded up to an odd number, lights up. The LEDs that light up gradually shifts towards the center led_num LEDs over a duration of 1700ms. 
"""
def show_direction_when_turning(degrees: int, led_num: int, led_state: bool): 
    global pixels
    led = number_remapper(degrees, minDeg, maxDeg, 0, 12)
    print(led)
    led_num = int(led_num)
    delay = calculate_delay(led)

    leds_to_be_on = calc_leds_to_be_on(led, led_num)
    turn_on_leds(leds_to_be_on, led_state)
   
    while(int(led) != int(num_led/2)):
        if (int(led) < num_led/2):
            led +=1 # moving to the right
            leds_to_be_on = calc_leds_to_be_on(led, led_num)
        elif (int(led) > num_led/2):
            led -=1 # moving to the left
            leds_to_be_on = calc_leds_to_be_on(led, led_num)
        print(led)
        
        turn_on_leds(leds_to_be_on, led_state)
        time.sleep(delay)


"""
Maps x from between in_min and in_max, to be the same relative place between out_min and out_max. The remapped value is constrainted to the range [out_min, out_max]
"""
def number_remapper(x: int, in_min: int, in_max: int, out_min: int, out_max: int):
    p = (x - in_min) * (out_max - out_min) / (in_max - in_min) + out_min
    if(p > out_max):
        p = out_max
    if(p < out_min):
        p = out_min
    return p

"""
Calculates which LEDs should be on given the led and number of leds to light up. 
"""
def calc_leds(direction, led_num): 
    if(led_num == 1): 
        out = [0]
        out[0] = int(direction)
    elif(led_num == 2): 
        out = [0] * 2
        out[0] = int(direction)
        out[1] = int(direction+0.5)
        if out[0] == out[1]: 
            out[1] = out[1]+1
    elif(led_num == 3): 
        out = [0] * 3
        out[1] = int(direction)
        out[0] = out[1]-1
        out[2] = out[1]+1
    elif(led_num == 4):
        out = [0] * 4
        out[1] = int(direction)
        out[2] = int(direction+0.5)
        if out[1] == out[2]: 
            out[2] = out[2]+1
        out[0] = out[1]-1
        out[3] = out[2]+1
    elif(led_num == 5): 
        out = [0] * 5
        out[2] = int(direction)
        out[1] = out[2]-1
        out[0] = out[1]-1
        out[3] = out[2]+1
        out[4] = out[3]+1
    elif(led_num == 6): 
        out = [0] * 6
        out[2] = int(direction)
        out[3] = int(direction+0.5)
        if out[2] == out[3]: 
            out[3] = out[3]+1
        out[1] = out[2]-1
        out[0] = out[1]-1
        out[4] = out[3]+1
        out[5] = out[4]+1
    elif(led_num == 7): 
        out = [0] * 7
        out[3] = int(direction)
        out[2] = out[3]-1
        out[1] = out[2]-1
        out[0] = out[1]-1
        out[4] = out[3]+1
        out[5] = out[4]+1
        out[6] = out[5]+1
    return out


"""
Calculates the delay between each shift in light-up LEDs based on how many shifts are needed. The duration is always 1700ms. 
"""
def calculate_delay(led_on: int): 
    number_of_leds = int(abs(num_led/2 - led_on)+0.5) # Rounding up and casting to int. 
    if (number_of_leds == 0):
        number_of_leds = 1
    delay = 1.7 / number_of_leds # The total time is always 1,7 seconds, so the delay is this amount split between the number of LEDs to be on. 
    return delay

"""
Main method to call when animating the LED strip when point-and-click rotating the view.
"""
def move(degree, led_num, led_state):
  if movement_queue:
    last_movement = movement_queue.pop()
    last_movement.raise_exception()
    last_movement.join()
  t1 = thread_with_exception('Thread 1', degree, led_num, led_state)
  t1.setDaemon(True)
#   t1.daemon = True
  movement_queue.append(t1)
  t1.start()  
  
"""
Method for turning the LEDs off
"""
def turn_LEDs_off():
    pixels.fill((10,10,10))
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

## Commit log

2024-08-06 initial frame ofr readme + License
2024-08-06 restructuring files
    [casting-bottom.stl, casting-side1.stl, casting-side2.stl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]
2024-08-06 adding the wheels
    [casting-bottom.stl, casting-side1.stl, casting-side2.stl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]
